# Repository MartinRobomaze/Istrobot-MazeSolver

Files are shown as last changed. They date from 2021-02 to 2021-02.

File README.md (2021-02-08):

# Istrobot-MazeSolver

## ESP32 PINOUT GUIDE
Before connecting anything to ESP32, check this link: https://randomnerdtutorials.com/esp32-pinout-reference-gpios/  
ESP32 has some piins which are not allowed to use because of integrated SPI flash(6-11), boot failing whe pulled high(12) and other strange things.
There are 2 more pins which are not allowed to use - pin 21 and 22 - these will be used for I2C distance sensors communication.  
**SENSOR_VP = GPIO36  
SENSOR_VN = GPIO39**

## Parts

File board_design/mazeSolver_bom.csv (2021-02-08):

Part | Value | Device | Package | Description | AVAILABILITY | DESCRIPTION | MF | MP | MPN | OC_FARNELL | PACKAGE | POPULARITY | PRICE | PURCHASE-URL | SPICEPREFIX
C1 | 100u | CPOL-EU140CLH-0810 | 140CLH-0810 | POLARIZED CAPACITOR, European symbol |  |  | RUBYCON |  | 100YXF100MEFC12.5X20 | 1144642 |  | 4 |  |  | C
C2 | 470u | CPOL-EU140CLH-0810 | 140CLH-0810 | POLARIZED CAPACITOR, European symbol |  |  |  |  |  | unknown |  | 4 |  |  | C
C7 | 22u | C-EUC1206 | C1206 | CAPACITOR, European symbol |  |  |  |  |  | unknown |  | 54 |  |  | C
C8 | 22u | C-EUC1206 | C1206 | CAPACITOR, European symbol |  |  |  |  |  | unknown |  | 54 |  |  | C
C9 | 22u | C-EUC1206 | C1206 | CAPACITOR, European symbol |  |  |  |  |  | unknown |  | 54 |  |  | C
C10 | 22u | C-EUC1206 | C1206 | CAPACITOR, European symbol |  |  |  |  |  | unknown |  | 54 |  |  | C
D1 |  | DIODE-DO214AC | DO214AC | DIODE |  |  |  |  |  | unknown |  | 14
F1 |  | 195591812 | C1812K | FUSE HOLDER
F2 |  | 195591206 | C1206K | FUSE HOLDER
IC1 | L293DD | L293DD | SO20 | PUSH-PULL FOUR CHANNEL DRIVER WITH DIODES |  |  |  |  |  | unknown |  | 2
IC2 | 7805TV | 7805TV | TO220V | Positive VOLTAGE REGULATOR |  |  |  |  |  | unknown |  | 57
J1 |  | CONN_02 | 1X02 | Multi connection point. Often used as Generic Header-pin footprint for 0.1 inch spaced/style header connections |  |  |  |  |  | unknown
L1 | DR125 | DR125 | DR125 | High Power Density, High Efficiency, Shielded Inductors |  |  |  |  |  | unknown |  | 1 |  |  | L
R1 | 4k7 | R-EU_R1206 | R1206 | RESISTOR, European symbol |  |  |  |  |  | unknown |  | 41 |  |  | R
R2 | 4k7 | R-EU_R1206 | R1206 | RESISTOR, European symbol |  |  |  |  |  | unknown |  | 41 |  |  | R
R3 | 4k7 | R-EU_R1206 | R1206 | RESISTOR, European symbol |  |  |  |  |  | unknown |  | 41 |  |  | R
R4 | 4k7 | R-EU_R1206 | R1206 | RESISTOR, European symbol |  |  |  |  |  | unknown |  | 41 |  |  | R
R5 | 4k7 | R-EU_R1206 | R1206 | RESISTOR, European symbol |  |  |  |  |  | unknown |  | 41 |  |  | R
R6 | 4k7 | R-EU_R1206 | R1206 | RESISTOR, European symbol |  |  |  |  |  | unknown |  | 41 |  |  | R
R13 | 4k7 | R-EU_R1206 | R1206 | RESISTOR, European symbol |  |  |  |  |  | unknown |  | 41 |  |  | R
R14 | 4k7 | R-EU_R1206 | R1206 | RESISTOR, European symbol |  |  |  |  |  | unknown |  | 41 |  |  | R
R21 | 10k | R-EU_R1206 | R1206 | RESISTOR, European symbol |  |  |  |  |  | unknown |  | 41 |  |  | R
U$1 | T-PLUG_CONNECTOR | T-PLUG_CONNECTOR | T_PLUG_CONNECTOR |  |  |  |  |  |  | unknown
U$2 | POLOLU_ENCODER | POLOLU_ENCODER | POLOLU_ENCODER
U$3 | POLOLU_ENCODER | POLOLU_ENCODER | POLOLU_ENCODER |  |  |  |  |  |  | unknown
U$4 | TDA9548 | TDA9548 | SOIC24L |  |  |  |  |  |  | unknown
U$5 | VL6180X | VL6180X | VL6180X |  |  |  |  |  |  | unknown
U$6 | VL6180X | VL6180X | VL6180X |  |  |  |  |  |  | unknown
U$7 | VL6180X | VL6180X | VL6180X |  |  |  |  |  |  | unknown
U$8 | BNO055 | BNO055 | BNO055
U$9 | T-PLUG_CONNECTOR | T-PLUG_CONNECTOR | T_PLUG_CONNECTOR |  |  |  |  |  |  | unknown
U1 | ESP32-DEVKITC-32D | ESP32-DEVKITC-32D | MODULE_ESP32-DEVKITC-32D | Eval Board For Esp-Wroom-32 Check prices | Warning | EVAL BOARD FOR ESP-WROOM-32 | Espressif Systems | ESP32-DEVKITC-32D |  |  | None |  | None | https://pricing.snapeda.com/search/part/ESP32-DEVKITC-32D/?ref=eda
U2 | AP1509-SOP8L | AP1509-SOP8L | SOP-8L | AP1509 |  |  |  |  |  | unknown

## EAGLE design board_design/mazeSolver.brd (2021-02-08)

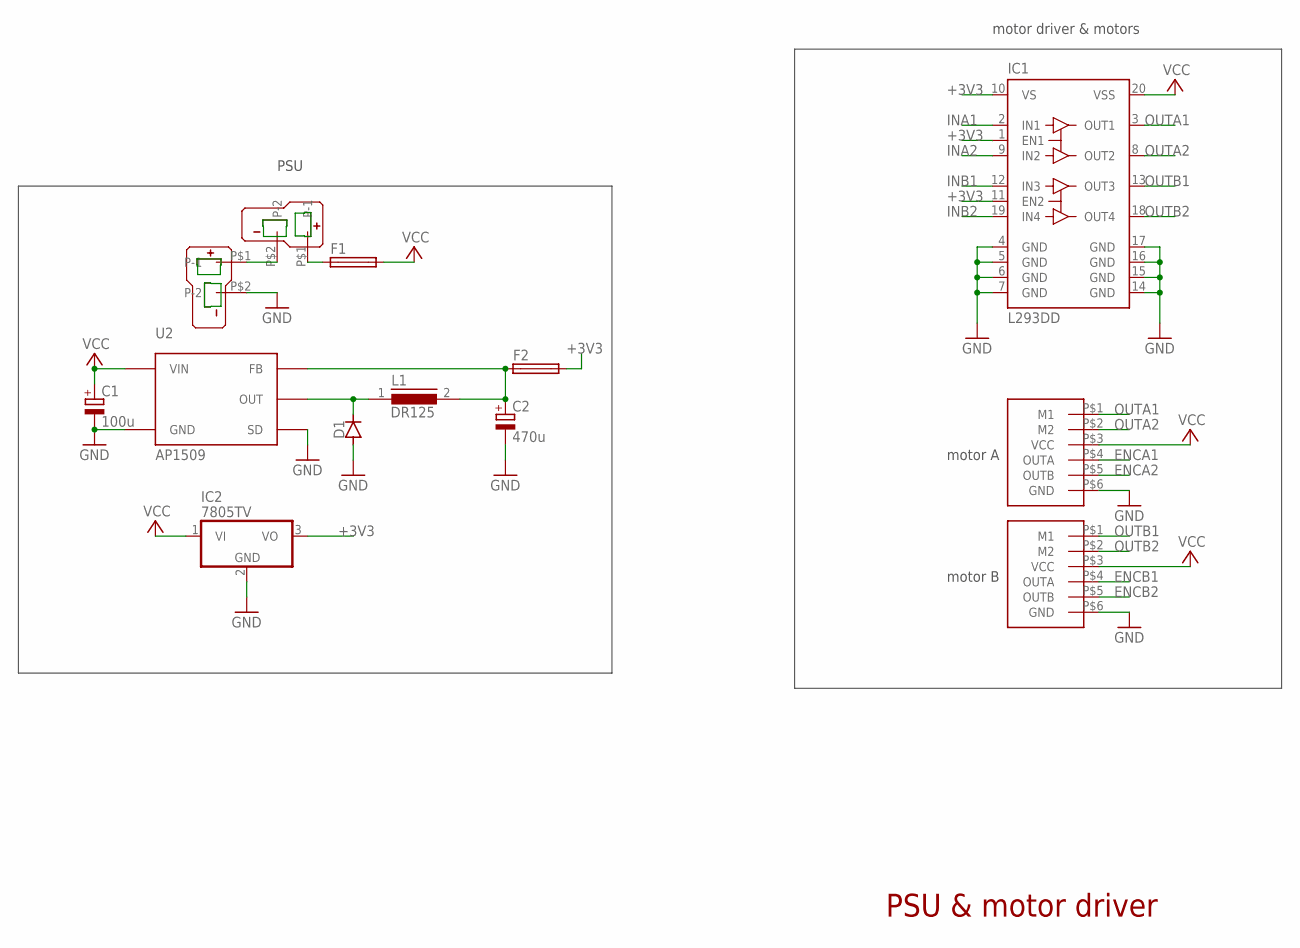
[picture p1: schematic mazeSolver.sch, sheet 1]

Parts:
C1: 100u; 140CLH-0810; MPN 100YXF100MEFC12.5X20
C2: 470u; 140CLH-0810
D1: DIODE-DO214AC; DO214AC
F1: 195591812; C1812K
F2: 195591206; C1206K
IC1: L293DD; SO20
IC2: 7805TV; TO220V
L1: DR125
U2: AP1509-SOP8L; SOP-8L
U$1, U$9: T-PLUG_CONNECTOR; T_PLUG_CONNECTOR
U$2, U$3: POLOLU_ENCODER

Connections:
+3V3: F2.2, IC1.1 (EN1), IC1.10 (VS), IC1.11 (EN2), IC2.3 (VO); also elsewhere on the board
ENCA1: U$2.P$4 (OUTA); also elsewhere on the board
ENCA2: U$2.P$5 (OUTB); also elsewhere on the board
ENCB1: U$3.P$4 (OUTA); also elsewhere on the board
ENCB2: U$3.P$5 (OUTB); also elsewhere on the board
GND: C1.-, C2.-, D1.A, IC1.4 (GND), IC1.5 (GND), IC1.6 (GND), IC1.7 (GND), IC1.14 (GND), IC1.15 (GND), IC1.16 (GND), IC1.17 (GND), IC2.2 (GND), U2.4 (SD), U2.5 (GND), U2.6 (GND), U2.7 (GND), U2.8 (GND), U$1.P$2 (P-2), U$2.P$6 (GND), U$3.P$6 (GND); also elsewhere on the board
INA1: IC1.2 (IN1); also elsewhere on the board
INA2: IC1.9 (IN2); also elsewhere on the board
INB1: IC1.12 (IN3); also elsewhere on the board
INB2: IC1.19 (IN4); also elsewhere on the board
unnamed: D1.C, L1.1, U2.2 (OUT)
unnamed: U$1.P$1 (P-1), U$9.P$2 (P-2)
unnamed: F1.1, U$9.P$1 (P-1)
unnamed: C2.+, F2.1, L1.2, U2.3 (FB)
OUTA1: IC1.3 (OUT1), U$2.P$1 (M1)
OUTA2: IC1.8 (OUT2), U$2.P$2 (M2)
OUTB1: IC1.13 (OUT3), U$3.P$1 (M1)
OUTB2: IC1.18 (OUT4), U$3.P$2 (M2)
VCC: C1.+, F1.2, IC1.20 (VSS), IC2.1 (VI), U2.1 (VIN), U$2.P$3 (VCC), U$3.P$3 (VCC)

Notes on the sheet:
motor A
motor B
motor driver & motors
PSU & motor driver
PSU

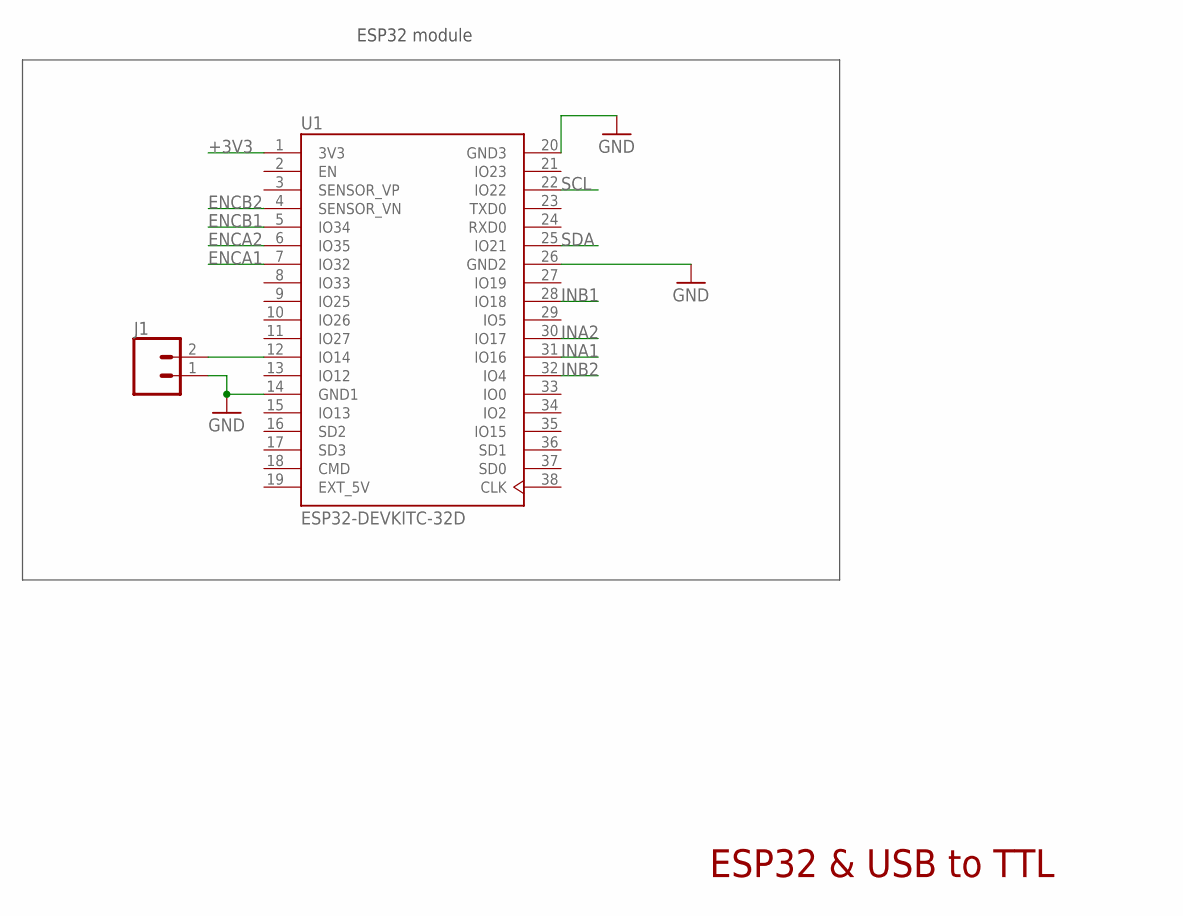
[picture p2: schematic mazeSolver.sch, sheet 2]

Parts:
J1: CONN_02; 1X02
U1: ESP32-DEVKITC-32D; MODULE_ESP32-DEVKITC-32D

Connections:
+3V3: U1.1 (3V3); also elsewhere on the board
ENCA1: U1.7 (IO32); also elsewhere on the board
ENCA2: U1.6 (IO35); also elsewhere on the board
ENCB1: U1.5 (IO34); also elsewhere on the board
ENCB2: U1.4 (SENSOR_VN); also elsewhere on the board
EXT_5V: U1.19 (EXT_5V)
GND: J1.1, U1.14 (GND1), U1.20 (GND3), U1.26 (GND2); also elsewhere on the board
INA1: U1.31 (IO16); also elsewhere on the board
INA2: U1.30 (IO17); also elsewhere on the board
INB1: U1.28 (IO18); also elsewhere on the board
INB2: U1.32 (IO4); also elsewhere on the board
unnamed: J1.2, U1.12 (IO14)
SCL: U1.22 (IO22); also elsewhere on the board
SDA: U1.25 (IO21); also elsewhere on the board

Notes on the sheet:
ESP32 & USB to TTL
ESP32 module

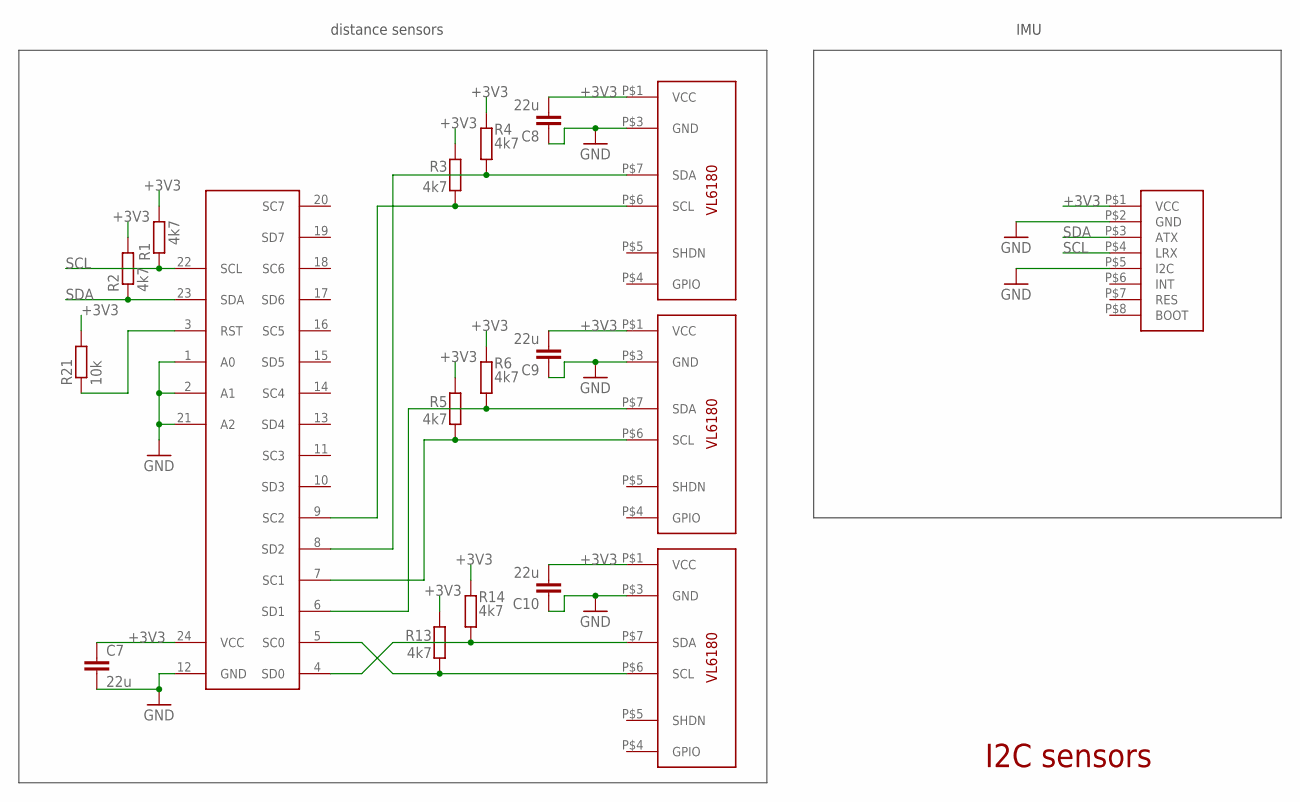
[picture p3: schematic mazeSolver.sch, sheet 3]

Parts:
C7, C8, C9, C10: 22u; C1206
R1, R2, R3, R4, R5, R6, R13, R14: 4k7; R1206
R21: 10k; R1206
U$4: TDA9548; SOIC24L
U$5, U$6, U$7: VL6180X
U$8: BNO055

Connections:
+3V3: C7.1, C8.1, C9.1, C10.1, R1.2, R2.2, R3.2, R4.2, R5.2, R6.2, R13.2, R14.2, R21.2, U$4.24 (VCC), U$5.P$1 (VCC), U$6.P$1 (VCC), U$7.P$1 (VCC), U$8.P$1 (VCC); also elsewhere on the board
GND: C7.2, C8.2, C9.2, C10.2, U$4.1 (A0), U$4.2 (A1), U$4.12 (GND), U$4.21 (A2), U$5.P$3 (GND), U$6.P$3 (GND), U$7.P$3 (GND), U$8.P$2 (GND), U$8.P$5 (I2C); also elsewhere on the board
unnamed: R13.1, U$4.5 (SC0), U$7.P$6 (SCL)
unnamed: R14.1, U$4.4 (SD0), U$7.P$7 (SDA)
unnamed: R6.1, U$4.6 (SD1), U$6.P$7 (SDA)
unnamed: R5.1, U$4.7 (SC1), U$6.P$6 (SCL)
unnamed: R4.1, U$4.8 (SD2), U$5.P$7 (SDA)
unnamed: R3.1, U$4.9 (SC2), U$5.P$6 (SCL)
unnamed: R21.1, U$4.3 (RST)
SCL: R1.1, U$4.22 (SCL), U$8.P$4 (LRX); also elsewhere on the board
SDA: R2.1, U$4.23 (SDA), U$8.P$3 (ATX); also elsewhere on the board

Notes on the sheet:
I2C sensors
distance sensors
IMU

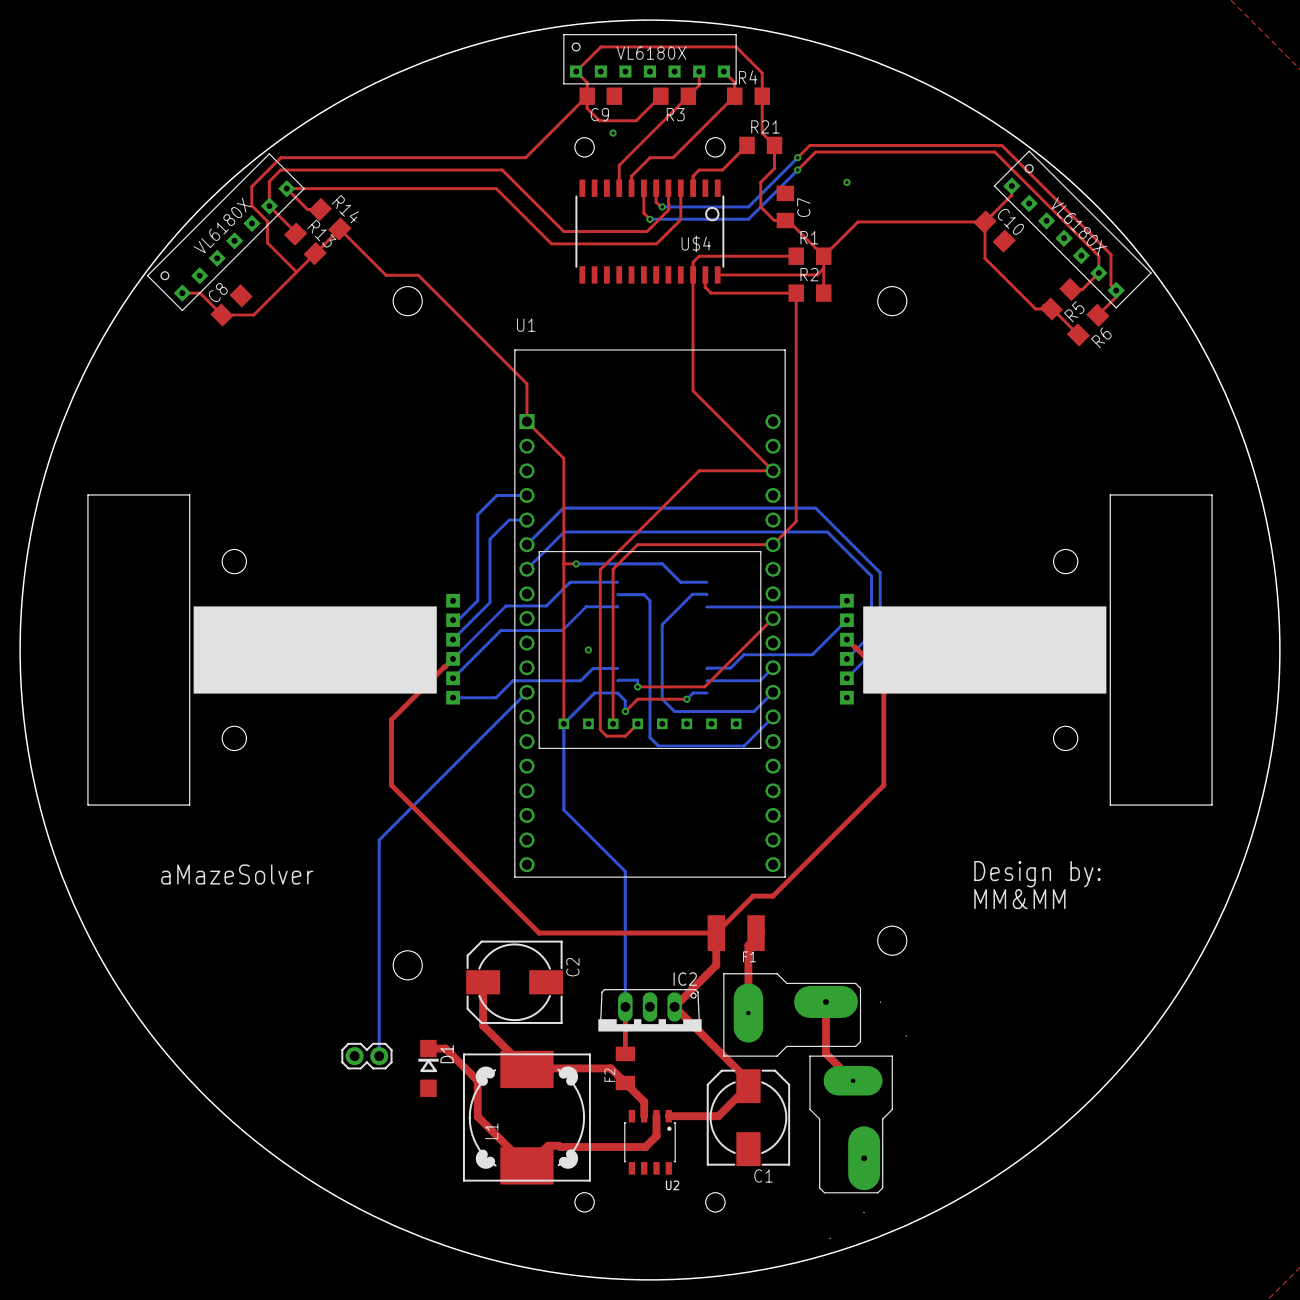
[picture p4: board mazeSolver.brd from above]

Board: 2 copper layers, 130.0 x 130.0 mm, 33 parts (1 on the bottom side), 29 nets.

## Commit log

2020-11-03 feature-4 | Schematic design for mazeSolver (#5)
    [mazeSolver.sch]
2020-11-04 Components placement
    [mazeSolver.brd, mazeSolver.sch]
2020-11-05 Added mounting holes
    [mazeSolver.brd]
2020-11-07 PCB Design
    [mazeSolver.brd, mazeSolver.sch]
2020-11-07 DRC Checks are passing
    [mazeSolver.brd, mazeSolver.sch]
2020-11-11 Added two 3d packages
    [mazeSolver.brd, mazeSolver.sch]
2020-11-12 A lot of changes
    [mazeSolver.brd, mazeSolver.sch]
2021-02-08 Board design changes
    [mazeSolver.brd, mazeSolver.sch]
2021-02-08 Added bom and gerbers
    [mazeSolver_bom.csv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]

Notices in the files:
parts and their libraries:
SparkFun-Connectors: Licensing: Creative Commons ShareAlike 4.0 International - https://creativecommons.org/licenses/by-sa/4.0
